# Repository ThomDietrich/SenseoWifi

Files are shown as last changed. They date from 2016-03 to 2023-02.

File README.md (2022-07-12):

# SenseoWifi - Smart Home Coffee Maker

Wifi'ify the Senseo coffee maker.

The coffee maker is with no doubt a central element of our lives.
In the Smart Home where every device is connected and automated, the coffee making can not be left out.
Let's bring the [Philips Senseo](https://de.wikipedia.org/wiki/Senseo) (Basic or Classic) into your Wi-Fi and control it remotely from your smartphone, through automation, or by extension via Alexa!

> Yes, this is silly, you should do it too!

## Summary

This project contains information and material regarding:

- Soldering a **custom PCB** needed to bring Senseo onto a Wi-Fi
- Connecting the custom PCB to the Senseo PCB
- Compiling firmware with [PlatformIO](https://platformio.org/) (e.g. as plugin in [VisualStudioCode](https://code.visualstudio.com/))
- Flashing the custom PCB with the **provided firmware**
- Connecting to Wi-Fi and [MQTT](https://www.hivemq.com/mqtt-essentials)
- Connecting to [Home Assistant](https://www.home-assistant.io), [openHAB](https://openhab.org) or any other home automation solution, including voice assistants like [Amazon Alexa](https://en.wikipedia.org/wiki/Amazon_Alexa)
- Adding a buzzer for **audio feedback** *(optional)*
- Adding a **cup detector** for further automation *(optional)*

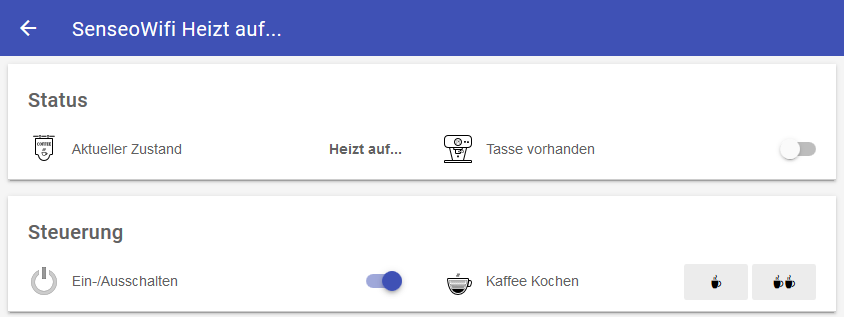
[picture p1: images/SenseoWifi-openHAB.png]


### Compatibility

This project is comatible with:

- Philips Senseo HD7810
- Philips Senseo HD7811
- Philips Senseo HD7812
- Philips Senseo HD7817
- Philips Senseo HD7865 Quadrante
- Philips Senseo HD7860 Quadrante
- … and most probably all similar models with one LED and three buttons

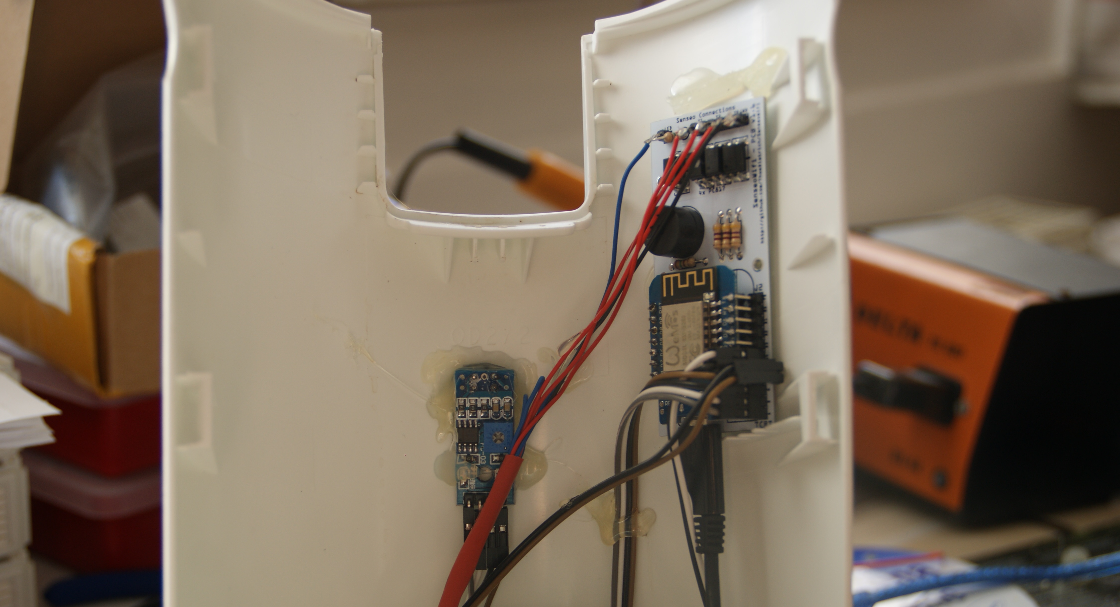
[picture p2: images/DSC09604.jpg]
installation example inside the machine


## Features

After implementing the steps below your Senseo coffee machine will offer the following new features.
This is especially useful in combination with a home automation system.

- Inform about the current state (Standby, Brewing, ...) of the machine
- Notify about an empty water tank
- Notify about a filled up coffee cup
- Remote control the machine via Wifi/MQTT commands
- Go through a complete brewing cycle automatically (Turn on, brew, turn off)
- Audio feedback via a built-in speaker
- Detect a cup via an optical sensor
- Collect usage statistics, e.g. stored in InfluxDB and visualized in Grafana

## Hardware Modification

The first challenge of this project is to hack the Senseo machine electronics.
You need to solder and connect a custom PCB to the machine.
In the end the PCB will not be visible from the outside, powered from the inside, connected via Wi-Fi and programmed over-the-air (OTA).

**⚠⚠⚠ Attention! For your own safety do not connect AC power while opened up. ⚠⚠⚠**

### Parts

| Part | Description |
|---|---|
| 1× Custom PCB | See [`SenseoWifi-PCB` folder](SenseoWifi-PCB) for schematic |
| 1× WeMos D1 Mini | Microcontroller, [learn more…](https://wiki.wemos.cc/products:d1:d1_mini) |
| 4× Sharp PC817 | Optocoupler interfacing with the Senseo board ([datasheet](http://www.sharp-world.com/products/device/lineup/data/pdf/datasheet/pc817xnnsz_e.pdf)). Thanks to these, the Senseo can be connected to AC power and to your PC via USB at the same time. Try to avoid this constellation and be cautious with active AC power. |
| 3× 470Ω Resistor | |
| 1× 1.5kΩ Resistor | |
| 1× Push button | To reset the microcontroller from the outside |
| 1× AC-DC Step Down Converter (220V to 5V) | As internally sourced power supply (e.g. [ebay.de](https://ebay.us/n9Cz6R) or [HLK-PM01](http://www.hlktech.net/product_detail.php?ProId=54)) |
| Generic male headers | A bunch of them |
| 1× Buzzer 12mm | *Optional* - Used for audio feedback, can be disabled in firmware (e.g. [reichelt.de](https://www.reichelt.de/Signalakustik/AL-60P01A/3/index.html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)) |
| 1× 150Ω Resistor | *Optional* - Size depends on buzzer |
| 1× TCRT5000 | *Optional* - To detect a cup. Reflective Optical Sensor, Regulated Module (e.g. [ebay.de](https://ebay.us/3Kf6fq)) |

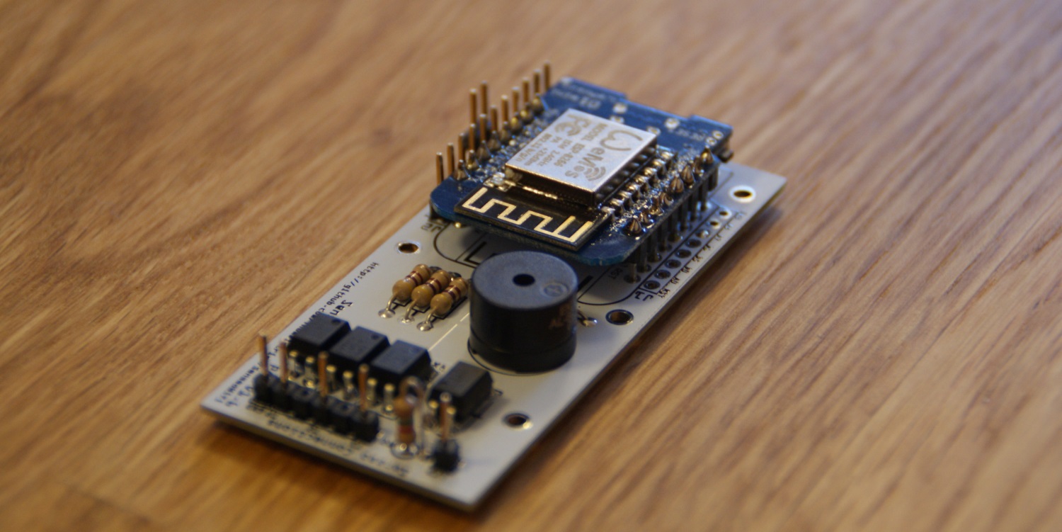
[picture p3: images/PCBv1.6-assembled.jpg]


**Power Consumption:**
The question was raised how much energy is consumed by the modification. The PCB consumes approx. 110mA.
Assuming the Senseo machine is connected to power 24/7, the additional electronics raise your electrical bill by 2.00€ per year.

### Steps

1. Solder the custom PCB according to the schematics provided in the `SenseoWifi-PCB` folder (designed in [Fritzing](http://fritzing.org))
2. Hot clue the custom PCB inside the Senseo machine in a free position [such as shown here](images/DSC09604.jpg)
3. Wire the custom PCB via the "Senseo Connections" header (angled pin headers recommended) to interface with the Senseo PCB. The solder pads to use for the LED, the buttons, and ground connection are shown on photos in the `images` folder, e.g., for the [Senseo Classic](images/DSC09627.jpg) and [Senseo Quadrante](images/SenseoQuadrante-PCB.jpg)
4. Connect a simple push button (the configuration reset button) to J3 and hot clue in the [base of the Senseo housing](images/resetbutton.jpg).
5. Connect the additional [power supply](images/DSC09646.jpg) to the Senseo power cable and wire to J4
6. Prepare a [small cutout](images/tcrt-cutout.jpg) in the Senseo front and [hot clue from behind](images/DSC09604.jpg). Connect to the TCRT header
7. Connect a USB cable to continue with firmware programming. Do not connect AC power

Please follow the details given in the schematics and the pictures in the [images](images) folder, which should make everything pretty clear.
Do not hessitate to create a support ticket on GitHub if we missed anything.
A pull request to improve this README is always welcome.

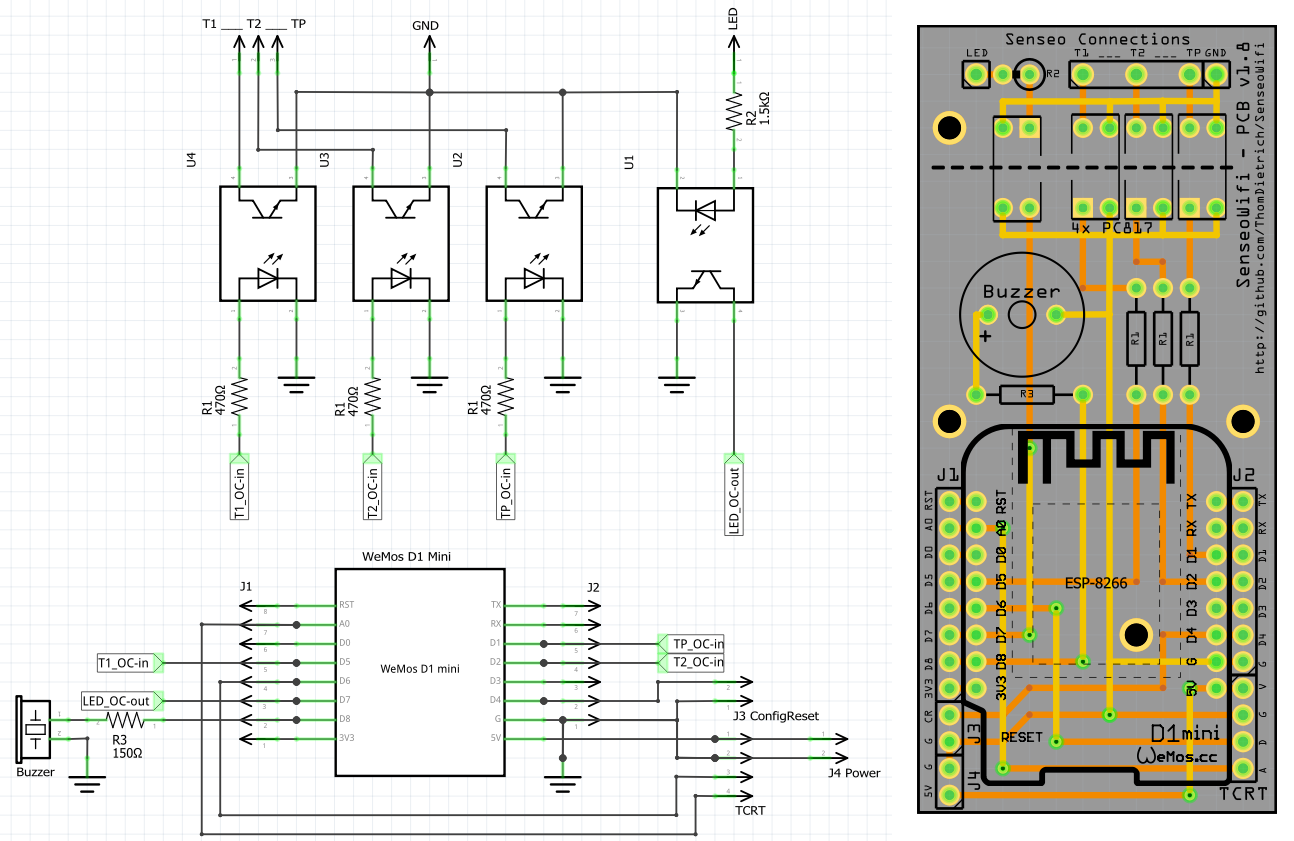
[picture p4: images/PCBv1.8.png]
schematics


## Firmware Upload

The WeMos microcontroller needs to be programmed with the code provided in this repository.
Be aware that the custom functionality is build on top of the excellent [Homie v3.0](https://github.com/homieiot/homie-esp8266/) framework.

An MQTT broker is needed in your network (e.g. mosquitto).

Please follow these instructions (last tested 2021-10-01):

1. Install PlatformIO via Visual Studio Code as decribed [here](https://platformio.org/platformio-ide) or upgrade your existing installation
2. Open PlatformIO and load a latest copy of this repository
3. Connect your Senseo via the USB cable to your PC (do not connect the Senseo to AC power!) and check the devices view of PlatformIO to verify
4. Transfer the firmware and the configuration web interface to the microcontroller.
  The full list of PlatformIO project tasks is:
   - Clean
   - Erase Flash
   - Build
   - Upload
   - Upload File System image
   - Monitor

   If any of the steps ends in a connection error dis- and reconnect the USB cable.
   You were successful when the monitoring terminal shows the SenseoWifi firmware version.
   For initial hardware testing see below.

5. Use a smartphone to connect to the provided Wifi, you will be redirected to a configuration web frontend
6. Provide your Wifi, MQTT, and other settings (we recommend the default homie base topic)
7. Use an MQTT client to inspect messages sent to the MQTT broker.
  You were successful when the message "senseo-wifi" is published to the topic `homie/senseo-wifi/machine/$name`
8. Disconnect the USB cable, close the Senseo housing, and connect the Senseo machine to AC power.
  The machine should once again start communicating via MQTT

**For Hardware testing:** A special piece of code is provided to test that your fresh hardware modifications are working.
Enable `testIO()` in `SenseoWifi.cpp` and check `testIO.cpp` for details.

**Configuration mode:** The configuration web frontend is only available when in configuration mode, i.e. when not yet configured.
Press the configuration reset button previously mounted in the base of the machine for 5 seconds to resets the firmware configuration.
The machine switches in configuration mode and provides a Wifi accesspoint, which upon connection once again presents the configuration web frontend.
Follow these instructions if you ever loose connection, or want to change your Wifi or MQTT settings.

### OTA Updates

After an initial flash with the firmware, updates can be sent via Wifi+MQTT, no need to take the machine apart.
The web frontend on flash and your custom configuration stay on the device.

```sh
python3 ota_updater_202011.py -l 192.168.0.75 -u user -d password -t "homie/" -i "senseo-wifi-rf21" .pio/build/senseo-wifi/firmware.bin
```

## Usage

If everything worked out your machine now communicates its status and accepts commands via MQTT.
You are now ready to interact with the machine and integrate it with other systems.
Please check the source code of `SenseoWifi.cpp` for details on states and commands.

## Smart Home Integration

With the machine connected to Wifi and MQTT, you can now link a smart home system to the important MQTT topics to integrate the machine with the rest of your smart home.

### Home Assistant Configuration Example

The following example integrates the Senseo machine with the home automation solution Home Assistant.
The configuration adds all necessary entities, translations to German, and clever automations to make the machine useful.
E.g. one automation enables a complete coffee brewing cycle with a single command, the other reminds you of your warm coffee every minute while you didn't pick it up.

Please make sure the machine is connected to your MQTT broker and adapt the machine name in the topic.

Home Assistant config file `packages/senseo_wifi.yaml`, see [`home-assistant/senseo_wifi.yaml`](home-assistant/senseo_wifi.yaml).

Lovelace configuration for an interactive UI control in the Home Assistant app:
```yaml
cards:
  - type: entities
    entities:
      - entity: switch.senseowifi_power
        name: Power
      - type: conditional
        conditions:
          - entity: sensor.senseowifi_opstate
            state_not: SENSEO_OFF
        row:
          entity: sensor.senseowifi_opstate
          name: Operationszustand
  - type: conditional
    conditions:
      - entity: binary_sensor.senseowifi_out_of_water
        state: 'on'
    card:
      type: entities
      entities:
        - entity: binary_sensor.senseowifi_out_of_water
          name: Wassertank leer
  - type: conditional
    conditions:
      - entity: switch.senseowifi_power
        state: 'on'
      - entity: binary_sensor.senseowifi_out_of_water
        state_not: 'on'
      - entity: binary_sensor.senseowifi_cup_full
        state: 'off'
    card:
      type: entities
      entities:
        - entity: binary_sensor.senseowifi_cup_available
          name: Tasse steht unter
  - type: conditional
    conditions:
      - entity: binary_sensor.senseowifi_cup_full
        state: 'on'
    card:
      type: entities
      entities:
        - entity: binary_sensor.senseowifi_cup_full
          name: Tasse gefüllt
  - type: conditional
    conditions:
      - entity: sensor.senseowifi_opstate
        state: SENSEO_READY
      - entity: binary_sensor.senseowifi_cup_available
        state: 'on'
      - entity: binary_sensor.senseowifi_cup_full
        state: 'off'
    card:
      type: entities
      entities:
        - type: buttons
          entities:
            - entity: input_boolean.senseowifi_brew_normal
              name: kleine Tasse brühen
              icon: mdi:coffee-to-go
            - entity: input_boolean.senseowifi_brew_double
              name: große Tasse brühen
              icon: mdi:coffee-to-go
title: SenseoWifi
type: vertical-stack
```

### openHAB Configuration Example

The following openHAB configuration allows integration of the Senseo machine with the home automation solution openHAB. Please make sure the machine is connected to your MQTT broker. Insert the MQTT broker IP and replace "senseo-wifi-home" by your device name in the below example.

The [expire binding](https://www.openhab.org/addons/bindings/expire1/) is recommended for debug-value.

**Note:** Not updated to latest firmware changes.

openHAB things file `mqtt.things`:
```
Bridge mqtt:systemBroker:LocalBroker [ host="your-broker-ip", secure=false ]
{
    Thing mqtt:topic:SenseoWiFi "SenseoWiFi" {
    Channels:
        Type string : Debug          "Debug"            [stateTopic="devices/senseo-wifi-home/machine/debug"]
        Type string : OpState        "Zustand"          [stateTopic="devices/senseo-wifi-home/machine/opState"]
        Type switch : OnOff          "OnOff"            [stateTopic="devices/senseo-wifi-home/machine/power", commandTopic="devices/senseo-wifi-home/machine/power/set", on="ON", off="OFF"]
        Type string : Brew           "Brew"             [stateTopic="devices/senseo-wifi-home/machine/brew",commandTopic="devices/senseo-wifi-home/machine/brew/set"]
        Type number : BrewedSize     "BrewedSize"       [stateTopic="devices/senseo-wifi-home/machine/brewedSize"]
        Type string : OutOfWater     "OutOfWater"       [stateTopic="devices/senseo-wifi-home/machine/outOfWater"]
        Type string : CupAvailable   "Tasse vorh."      [stateTopic="devices/senseo-wifi-home/machine/cupAvailable"]
        Type string : CupFull        "Tasse voll"       [stateTopic="devices/senseo-wifi-home/machine/cupFull"]
        Type string : Online         "Online"           [stateTopic="devices/senseo-wifi-home/$online"]

        Type string : version        "Version"          [ stateTopic="devices/senseo/$homie"]
        Type string : name           "Name"             [ stateTopic="devices/senseo/$name"]
        Type string : ip             "IP-address"       [ stateTopic="devices/senseo/$localip"]
        Type string : mac            "MAC-address"      [ stateTopic="devices/senseo/$mac"]
        Type string : fw_name        "Firmware Name"    [ stateTopic="devices/senseo/$fw/name"]
        Type string : fw_version     "Firmware Version" [ stateTopic="devices/senseo/$fw/version"]
        Type string : nodes          "Nodes"            [ stateTopic="devices/senseo/$nodes"]
        Type string : implementation "Implementation"   [ stateTopic="devices/senseo/$implementation"]
        Type string : interval       "Update interval"  [ stateTopic="devices/senseo/$stats/interval"]
    }
}
```

openHAB items file `SenseoWifi.items`:
```
String KU_Senseo_Debug         "Debug [%s]"                          {channel="mqtt:topic:SenseoWiFi:Debug", expire="10s"}
String KU_Senseo_OpState       "Zustand [MAP(senseo-wifi.map):%s]"   {channel="mqtt:topic:SenseoWiFi:OpState"}
Switch KU_Senseo_OnOff         "OnOff"                               {channel="mqtt:topic:SenseoWiFi:OnOff"}
String KU_Senseo_Brew          "Brew"                                {channel="mqtt:topic:SenseoWiFi:Brew"}
Number KU_Senseo_BrewedSize    "BrewedSize"                          {channel="mqtt:topic:SenseoWiFi:BrewedSize"}
String KU_Senseo_OutOfWater    "OutOfWater"                          {channel="mqtt:topic:SenseoWiFi:OutOfWater" [profile="transform:MAP", function="senseo-wifi.map"]}
String KU_Senseo_CupAvailable  "Tasse vorh."                         {channel="mqtt:topic:SenseoWiFi:CupAvailable" [profile="transform:MAP", function="senseo-wifi.map"]}
String KU_Senseo_CupFull       "Tasse voll"                          {channel="mqtt:topic:SenseoWiFi:CupFull" [profile="transform:MAP", function="senseo-wifi.map"]}
String KU_Senseo_Online        "Online"                              {channel="mqtt:topic:SenseoWiFi:Online"}
```

openHAB sitemap example `SenseoWifi.sitemap`:
```
sitemap testing label="Senseo-Tests"
{
    Text item=KU_Senseo_Online label="Fehler [Maschine nicht verfügbar!]" visibility=[KU_Senseo_Online == "false"] valuecolor=["false"="red"]
    Frame label="Status" visibility=[KU_Senseo_Online == "true"] {
        Text item=KU_Senseo_OpState label="Aktueller Zustand"
        Default item=KU_Senseo_Debug      label="Debug" visibility=[KU_Senseo_Debug != UNDEF] valuecolor=["red"]
        Text item=KU_Senseo_OutOfWater label="Wassertank [Leer]" visibility=[KU_Senseo_OpState == SENSEO_NOWATER] valuecolor=[ON="maroon"] icon="water"
        Switch item=KU_Senseo_CupAvailable label="Tasse vorhanden" icon="coffee_cup"
        Switch item=KU_Senseo_CupFull label="Tasse voll" visibility=[KU_Senseo_CupAvailable == ON] icon="coffee_cup_hot"
    }
    Frame label="Steuerung" visibility=[KU_Senseo_Online == "true"] {
        Switch item=KU_Senseo_OnOff label="Ein-/Ausschalten"
        Switch item=KU_Senseo_Brew label="Kaffee Kochen" mappings=[1cup="☕", 2cup="☕☕"]
    }
}
```

## Contribution

Further details outstanding. Don't hesitate to open a support issue!

Happy Hacking!

----

# Disclaimer and Legal

> *Philips* and *Senseo* are registered trademarks of *Philips GmbH*.
>
> This project is a community project not for commercial use.
> The authors will not be held responsible in the event of device failure or bad tasting coffee.
>
> This project is in no way affiliated with, authorized, maintained, sponsored or endorsed by *Philips* or any of its affiliates or subsidiaries.

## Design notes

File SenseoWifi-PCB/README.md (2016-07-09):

# SenseoWifi-PCB

this folder contains the PCB design, needed for this project.

Designed in [Fritzing](http://fritzing.org/download) (min. Version 0.9.3b, `fritzing parts` newer 2016-07-10)

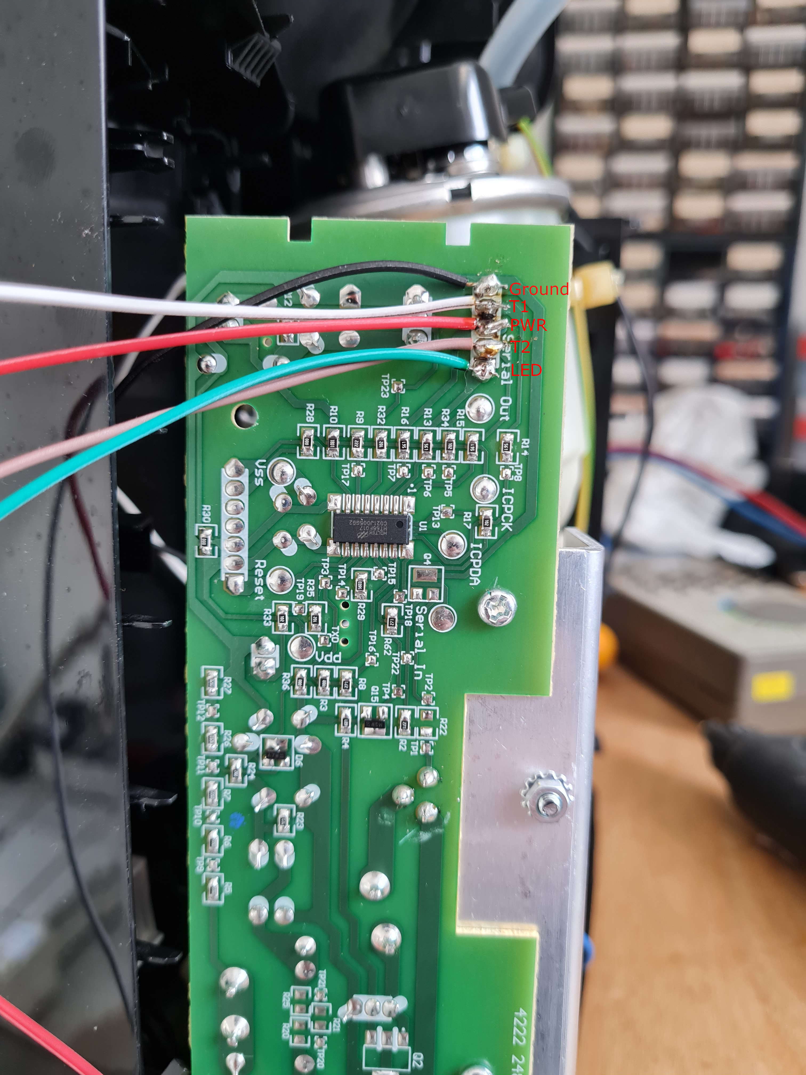
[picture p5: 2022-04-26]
images/SenseoQuadrante-PCB.jpg

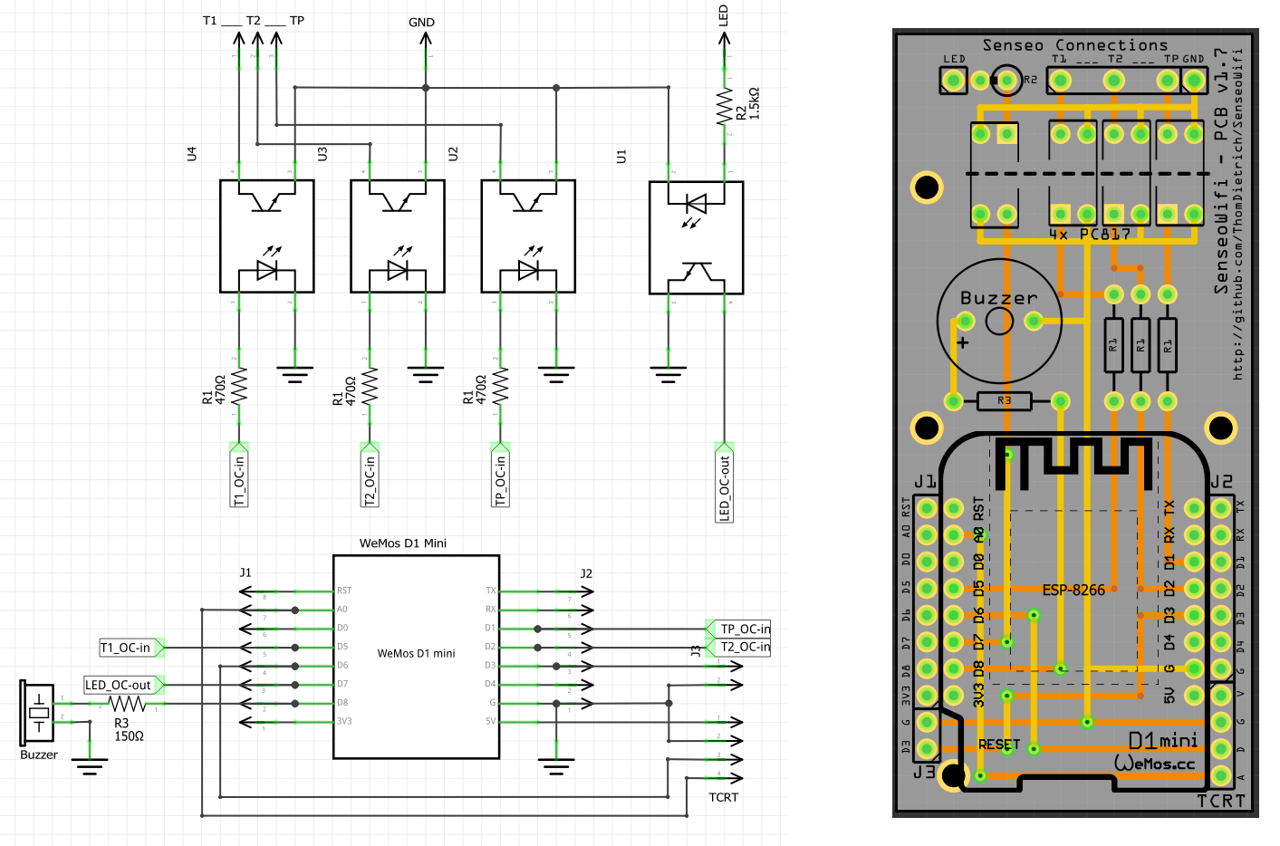
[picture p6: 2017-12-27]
images/PCBv1.7.png

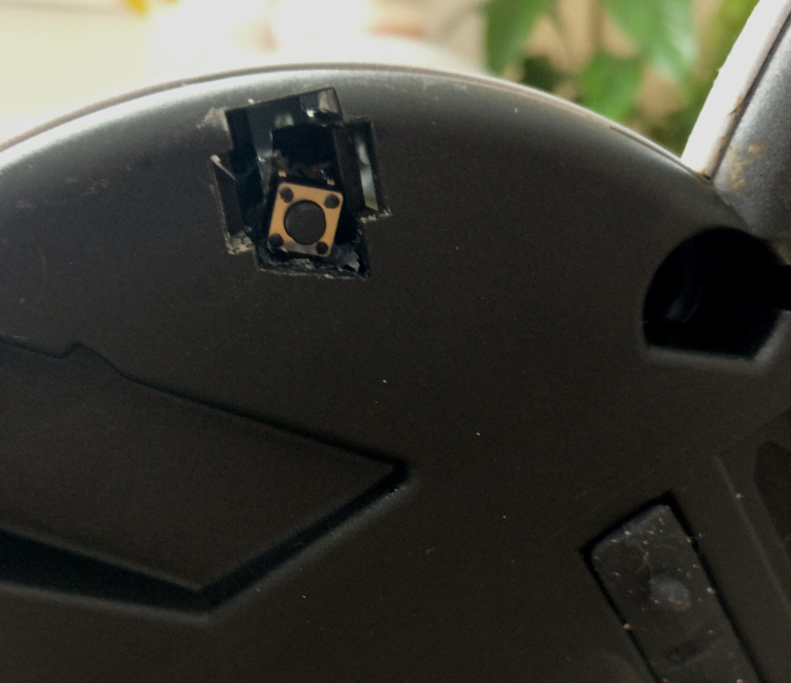
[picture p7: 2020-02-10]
images/resetbutton.jpg

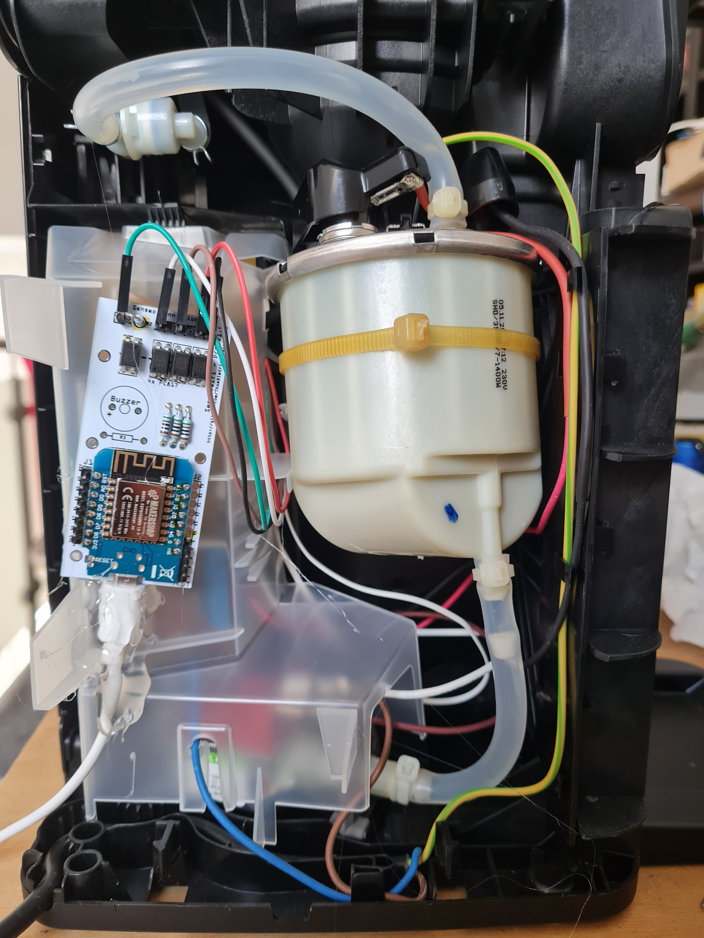
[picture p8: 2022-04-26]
images/SenseoQuadrante-Mount.jpg

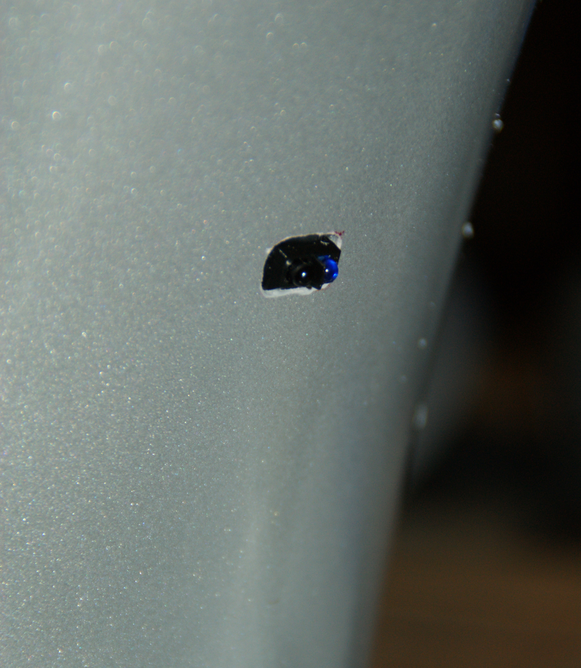
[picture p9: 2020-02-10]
images/tcrt-cutout.jpg

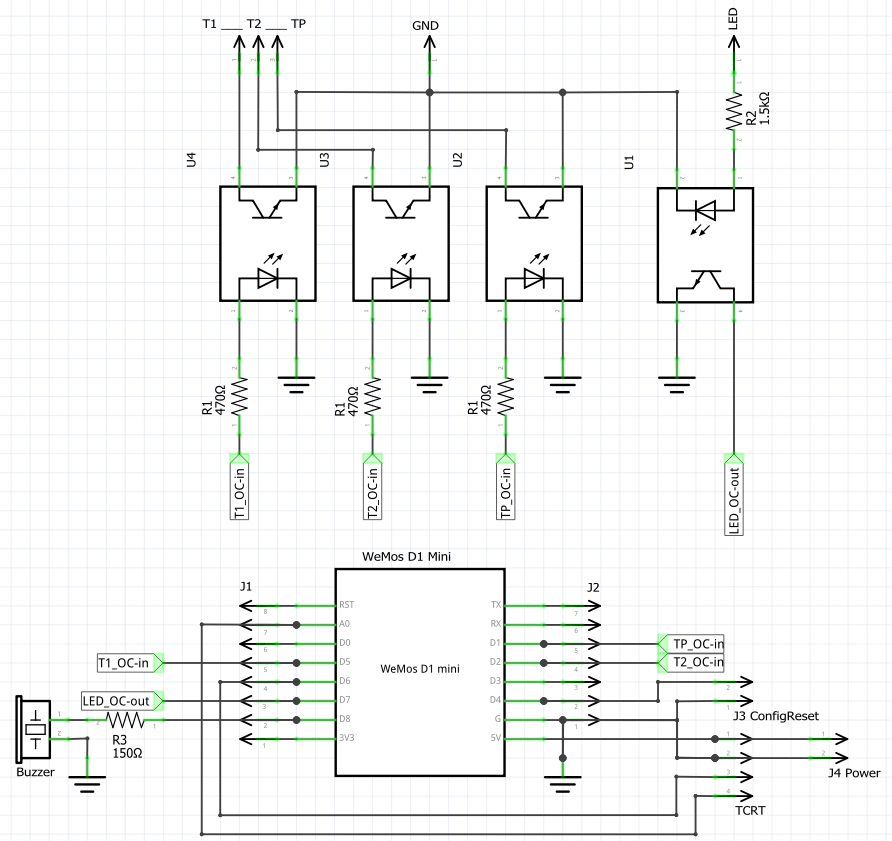
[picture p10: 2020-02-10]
images/PCBv1.8-circuit.png

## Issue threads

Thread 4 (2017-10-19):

Add README

ThomDietrich, 2017-10-19:
A README with a short description, build and usage instructions needs to be added!

@guybrushix out of coincidence I saw your forking of the repository. The README is currently missing but the PCB+code are doing their job just great since one year in two machines. Do you need any help?

guybrushix, 2017-10-20:
Thank you, I first try on my own.

VinceMasuka, 2018-09-13:
I'm doing this with FHEM instead of openHAB2. Therefore some words about the MQTT functionality would be helpful. Of course it's to be read within the src files, but a litte documentation would surely help to understand readings and commands (without misinterpretation).

fredericdepuydt, 2019-01-30:
The README file currently doesn't describe the use of PlatformIO as IDE.
Took me some time before I realized the Arduino IDE wasn't the way to program the ESP8266

mboremski, 2019-07-12:
Would also like som more advice on how to bring up.
Took me some hours of research ti find hiw to get the code onto the ESP8266.
Finally found **PlatformIO** as solution.

Than it took some time to get the right libs installed and go on with compiling.
e.g. ArduinoJson has to be 5.x.x. Seems 6.x.x does some things different and wount compile.

Than tried to monitor the connected device, but default baudrate of 9600baud issn't right
So I had to add this to platformio.ini:
`monitor_speed = 115200`

With this I have been able to debug some problems with the homie/config.json

Now I am struggeling on implementing the node in openhab.
Your device uses Homie 2.x.x, but Openhab (now) wants 3.x.x thats (as far as I could figure out) not released for esp8266.
It looks like it can be added via a *.things-File manually.
Maybe you could share the neccesary steps with us?

fredericdepuydt, 2019-07-12:
@ThomDietrich Just clarifying it's build using PlatformIO, and a link to https://platformio.org/ would suffice.

@mboremski You can take a look in the development branch of homie (https://github.com/homieiot/homie-esp8266/tree/develop-v3). I'm currently still using homie 2.0 as well, and I've added the MQTT topics manually in my OpenHAB. As for the libs, when using PlatformIO in VSCode all libs are imported automatically. The baudrate can be found in 'src/SenseoWifi.cpp': `Serial.begin(115200);` (but it wouldn't do any harm if this were added in the README as well).

Kind regards,
Frederic Depuydt

mboremski, 2019-07-12:
tried to switch to dev-v3 for homie but than got a bunch of errors I cant't handle.
e.g.
```
{
	"resource": "/d:/SenseoWifi-master/src/SenseoWifi.cpp",
	"owner": "cpp",
	"severity": 8,
	"message": "no matching function for call to 'HomieNode::HomieNode(const char [8], const char [8])'",
	"startLineNumber": 22,
	"startColumn": 42,
	"endLineNumber": 22,
	"endColumn": 42
}
```
and
```
{
	"resource": "/d:/SenseoWifi-master/src/SenseoWifi.cpp",
	"owner": "_generated_diagnostic_collection_name_#0",
	"severity": 8,
	"message": "no instance of constructor \"HomieNode::HomieNode\" matches the argument list -- argument types are: (const char [8], const char [8])",
	"startLineNumber": 22,
	"startColumn": 22,
	"endLineNumber": 22,
	"endColumn": 22
}
```
fogot to say:
espressif8266 > 2.0.4 also generates some problems.
Needed to change platform in platformio.ini to:
`platform = espressif8266@2.0.4`

would you share your files with us to help bring it up?
looking for things-file, map-file and sitemap-file(sniped)

mboremski, 2019-07-13:
Have a look at #19 to see some config-example for OH  2.4.0 ;-)

ThomDietrich, 2020-02-08:
Hey guys, I've updated the README to include flashing instructions and other details. Please open a new issue for whatever you run into

Closed 2020-02-08.

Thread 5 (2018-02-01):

Detect correct brewedSize regardless following state

ThomDietrich, 2018-02-01:
So far the information wether a small or big cup was brewed is wrongfully calculated when the machine switches into NOWATER or OFF state right after brewing. Fix to:

> Send "1" or "2" on topic `brewedSize`, regardless the following state. Otherwise send "0".

ThomDietrich, 2018-02-01:
Fixed in https://github.com/ThomDietrich/SenseoWifi/commit/7e8563480429ca54c16e6de5afd2ae5411a366e6

Closed 2018-02-01.

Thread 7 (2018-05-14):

test environment starts to beep immediately after flash

VinceMasuka, 2018-05-14:
Hi

I just rebuild your project. Right after flashing the buzzer starts to beep quiet annoying. Of corse I want to test the board before I start to integrate it into the Senseo. That's why I connect 5V and GND only to start WiFi. Although there is WiFi showing up now and I got it configured (no idea why it did not used the config.json besides), there unfortunately is this noisy beep again. Perhaps it's just my confused, deaf ears for the moment, but right now I'm kind of clueless what this thing wants to tell me...

Suggestions? Anyone?

Thanks!

Regards
Vince

ThomDietrich, 2018-05-15:
Hey!
Well that shouldn't happen but it is along time since I last flashed without a connection to the machine. Is the beeping continuous?

My suggestion would be to 1) check the serial console and/or the MQTT broker to learn about the state of the program. Besides that, 2) you could disable the buzzer in the initial configuration custom settings.

VinceMasuka, 2018-07-01:
Sorry... I was like unable to work with this project for the past several weeks...

Yes, it beeps continously. I think I leave this issue at "continous improvement process". Means that I unsoldered the beeper for silent's sake and try to get the rest running and build in the Senseo until I get back to this. Perhaps it's like you said and only an issue if it's not build in.

ThomDietrich, 2018-07-02:
I'd suggest to first connect everything and then check the serial console for debugging/log ouptut. You'll learn about the actions of the program. A constantly beeping of the beeper tells me that you probably did not yet flash my source code onto the chip. There is no continuous beeping in my code...

Closed 2020-02-08.

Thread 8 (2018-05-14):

what plug to power this

VinceMasuka, 2018-05-14:
Hi

Sorry for the maybe dumb question, but looking at the board layout, the used pins and comparing lab plus final pictures of yours...
What plug(s) are responsible for powering (5V and GND) this board?
Do you power it solely by USB?
And if so: Did you connect that USB directly to the 220V to 5V AC-DC step down module?

Thanks!

Regards
Vince

ThomDietrich, 2018-05-15:
Good question, we left the USB port open for debugging and connected the step down module directly to `GND` and `5V`. Now that you ask: I am not quite sure why there are no dedicated pins for this purpose.
Looking at the pictures, I believe that the hacked extra connectors on the side serve that purpose in our machine. https://raw.githubusercontent.com/ThomDietrich/SenseoWifi/master/images/DSC09604.jpg
If you build and soldered your own PCB, it should be easy to add additional pins. As for our provided PCB design: Yes we should improve it...

Closed 2018-07-01.

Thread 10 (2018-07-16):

Error in fz-File (fritzing 0.9.3b on Windows 10)

evildrummer, 2018-07-16:
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

ThomDietrich, 2018-07-16:
Nope sorry must be an issue with your system or download. Just tested with a fresh Fritzing and file download myself.

evildrummer, 2018-07-16:
Hm,

i tested it on Win7 and 10 (x86 and x64 Version). :-/

Can you upload a fzz or gerber version of the File? Then i dont need Fritzing anymore.
Fzz is the supported type when i want to upload it on their Website (aisler.net).

Thanks

ThomDietrich, 2018-07-16:
[SenseoWifi-PCB_GERBER.zip](https://github.com/ThomDietrich/SenseoWifi/files/2197631/SenseoWifi-PCB_GERBER.zip)

This is the file I last used to produce PCBs I'm currently using. Be aware that I realized later on that two connectors are mission in this version https://github.com/ThomDietrich/SenseoWifi/issues/8#issuecomment-389109496

ThomDietrich, 2018-07-16:
You should try once again. Your error sounds like you did something wrong when downloading the file...

evildrummer, 2018-07-16:
Well. Finally i was able to open it :)

but!..... i´m not sure if my added pins are well placed :)
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

If you´re giving me an ok i´ll do the pull request. But first i have to check out what that means :) I´m new on github.

ThomDietrich, 2018-07-16:
Looks fine to me. I myself was hoping to not extend the size of the PCB... you know what, give me a sec.

ThomDietrich, 2018-07-16:
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

ThomDietrich, 2018-07-16:
[SenseoWifi_PCB_v1.7_Extended_Gerber.zip](https://github.com/ThomDietrich/SenseoWifi/files/2198093/SenseoWifi_PCB_v1.7_Extended_Gerber.zip)

ThomDietrich, 2018-07-16:
The new connectors on the bottom left are for the Reset button and for VCC from the step down converter. Enjoy! Let me know if you need more help!

mboremski, 2019-07-20:
@ThomDietrich might be closed.. not? :-)

ThomDietrich, 2019-07-22:
Sounds like it. Thanks ;)

Closed 2019-07-22.

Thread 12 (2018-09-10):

(Improvement) Replace Step Down AC-DC Converter (220V to 5V) by Hi-Link-ac-dc

diogopms, 2018-09-10:
Note: This is not a real issue, but an improvement to the PCB.

What do you think, about changing to:
https://pt.aliexpress.com/item/Hi-Link-ac-dc-power-module-5v-3w-220v-isolated-ac-dc-converter/32360232521.html

VinceMasuka, 2018-09-13:
Works flawlessly. I took the same on my setup.
[http://www.hlktech.net/product_detail.php?ProId=54](url)

ThomDietrich, 2018-11-21:
Looks good indeed. Why would you recommend this one over the one I've linked?

VinceMasuka, 2018-12-17:
Perhaps because it comes in a enclosure?
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
(inside it's pretty much the same, I guess)

Actually that might be preferable of sorts, as there is water around and you might would like the idea of some extra "shielding"...

ThomDietrich, 2018-12-17:
Fine by me. Please create a PR against the README.md as an alternative product in the components table.

Ditoxius, 2019-01-17:
Hi, i have another question regarding the supply voltage.

The senseo µC is powered the whole time with 5V via a capacitive divider and zener diode. Have you tried using its supply voltage to power the WeMos module instead of installing a separat step-down converter?

Thank you for your project....i hope to make my coffee maker smart, soon :D

ThomDietrich, 2019-01-18:
Yes. I tried and I did a few thought experiments on the topic with colleagues. The problem is (please correct me if you disagree) that such a circuit has a narrow operating point and experiments showed that voltage drops as soon as more than a few milliamps are consumed.

Another problem is the missing divide of electrical potentials between the Senseo supply and the USB connection (think optocouplers).

I very much prefer the decoupled solution for its simplicity and the flexibility in build in troubleshooting. Lastly and maybe most importantly: The solution comes as safe as it can get (I hope :) ).

Closed 2019-01-18.

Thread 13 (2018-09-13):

current on the buttons

VinceMasuka, 2018-09-13:
Hi...

I tried to get this project finally done and everything is now build in the Senseo:

- MQTT nicely reports the readings

- MQTT readings instantly update themselves when you send a MQTT command or

- MQTT readings instantly update themselves when press a button on the Senseo

But:

- a MQTT send "power" to the board reports that Senseo is powered, but it won't turn on (harware button works of course)

- strangely all buttons on the board (TP, T1, T2) allways have current of exactly 5.08 volts (no matter if MQTT says they are on or not) (I expected something like 0 volts when it's turned off)

By any chance you can't push me in the right direction what to check first?

Thanks!

Regards
Vince

ThomDietrich, 2018-11-21:
Hey Vince!
Sorry for the late reply. Did you solve the issue?

ThomDietrich, 2018-12-14:
Hey!
Just to summarize:

1. You receive MQTT messages from the board and therefore are certain that the firmware flash worked.
2. More precisely, you receive "ON" via `.../power` and "SENSEO_HEATING" via `.../opState` if you press the power button manually?
3. You publish a message with payload "ON" to the topic `.../power/set` and "MQTT reports back" - what do you mean by that? As you can see [here](https://github.com/ThomDietrich/SenseoWifi/blob/master/src/SenseoWifi.cpp#L45) there is no optimistic response. The response should be what's described under (2.). For testing please send an invalid payload and check for the "power: malformed message content." debugging message.

To rule out hardware issues you could modify the source code to trigger a power press, e.g., when the firmware has booted.

ThomDietrich, 2018-12-14:
FYI:
Try to get it working with MQTT first. That is best for troubleshooting.
For later use you might be happy to find my openHAB configuration here: https://github.com/ThomDietrich/openhab-config/blob/master/items/senseoWifi.items
Don't torture yourself with FHEM 😅

VinceMasuka, 2018-12-16:
1. I really like to belive that.
2. Yes, that works as expected. If I manually push the button physically on the Senseo, my mosquitto_sub tells me "opState SENSEO_HEATING", "power ON", "outOfWater false", "brew false" and "opState SENSEO_READY".
3. Oh, I just meant if I publish something, that the mosquitto subscription immediately tells me so (as expected). So when I send a invalid content like
"mosquitto_pub -t homie/Senseo/machine/power/set -m toggle"
I receive:
"debug power: malformed message content. Allowed: [ON,OFF]"

That brings us to the assumed valid version:
mosquitto_pub -t homie/Senseo/machine/power/set -m ON
...but "opState" stays on "SENSEO_OFF".

ThomDietrich, 2018-12-16:
So far so good. Now I'm afraid you need to modify the source code to figure out where the issue lies exactly.

VinceMasuka, 2018-12-17:
OK, for the sake of progress, I'll have to do so...

So this suggestion implies that you think this is not hardware, but software related?

ThomDietrich, 2018-12-17:
To the contrary. As the firmware seems to work and interact with your machine (it's able to detect "power ON") this is most probably an issue with your hardware setup. You need to follow along the route, make sure the optocoupler is swithced and check why it doesn't trigger a Senseo button press. One thing you could do: Increase the milliseconds of virtual button press, then measure the optocoupler on output side. Whatever you do please be careful with high voltage.

VinceMasuka, 2018-12-18:
Nice hint. I modified the virtual button press to 1000 an voila: Senseo is powering up.

Thanks!

ThomDietrich, 2018-12-19:
Wonderful. Would you invest a few extra minutes to figure out which lowest value would work for you? I'd like to update the source code here accordingly but one full second is quite a lot. How about e.g. 150 or 200?

VinceMasuka, 2018-12-19:
As to your pictures and decriptions, having your project as example for mine, I directly added an external micro usb access to my 7820 Senseo, too. This makes flashing pretty easy now and I'll do some more flashes (see my open TCRT issue). With this upcomming flashing, I'll alter the virtual press button and report back within this thread.

ThomDietrich, 2018-12-19:
Thanks! Your help will make a rebuild easier for the next guy.

I need to update documentation. I know that it does not at all cover all aspects of the project.
Regarding OTA I can tell you that you need to follow the OTA mechanism of homie-esp8266:

* http://marvinroger.github.io/homie-esp8266/docs/stable/others/ota-configuration-updates/

If the script doesn't work for you check out this bash script: https://github.com/marvinroger/homie-esp8266/issues/308

VinceMasuka, 2018-12-21:
I don't know what went wrong in first place, but it now seems that my setup accepts much lower ms for the virtual button press than before (I'm starting to suspect a faulty copper wire in there...).

Anyhow it looks like that
    _static const int pressDuration = 36;_
is the lowest working value with the Seseno 7820.

mboremski, 2019-07-15:
Not sure if this still is open..
I also had some issues to get the buttons "pressed" via OP.
For me 110ms have been the lowest value it was working with.
I would recommend to change it to:

```cpp
// Duration of button "press" (in milliseconds)
static const int pressDuration = 150;
```

ThomDietrich, 2019-07-19:
It is probably safe to assume that this change will not have any side effects. I would be most curious to know why this is an issue for you guys. Do you own an older/newer Senseo model or did you use different optocouplers?

mboremski, 2019-07-20:
From my knowledge of µC coding it **might** be possible that Senseo changed the time a button needs to be pressed. Maybe for better antibeat performance.
I think the 100ms has been a bit to tight to fir for all devices.

Did you once try to shorten your `pressDuration` to find the minimum pressing-time for your Senseo?
Could be that 90ms already is to short. In this case the 100ms are to tight to adress also manufacturing-tolerances.

ThomDietrich, 2019-07-22:
I probably did. My initial tests to understand the behavior of the machine were pretty thorough. Can't remember though and your 90ms argument could just as well be true. 150 is a worthy improvement 👍

Closed 2019-07-22.

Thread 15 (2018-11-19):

publishes to MQTT but does not receive

vogler, 2018-11-19:
I'm using home-assistant's embedded MQTT broker. The esp8266 publishes topics like `opState` and `debug`, but doesn't receive any commands. My Tasmota devices receive commands via MQTT jut fine.
Publishing `foo` to `devices/senseo-wifi/machine/power` should result in an output on `devices/senseo-wifi/machine/debug`, but doesn't do anything.
How can I debug this?

vogler, 2018-11-19:
Ok, just found out it's actually `devices/senseo-wifi/machine/power/set`. Works 😄
Maybe a sentence in the readme on how to test it would be a good idea.

ThomDietrich, 2018-11-21:
The README does not explicitly state that but the device follows the Homie convention. Check it out for all details! ;)

I'll need to update the README with a lot of things. Anything else you found? Does your machine work? Btw if you are located in Germany I could send you one of my spare PCBs.

ThomDietrich, 2018-11-22:
Hey!
You can leave USB connected for debugging, that is the main reason for the optocouplers.

What concerns me is the picture of your machine. It seems to be an older model. Could you tell me the exact type number?
Nevertheless, as the PCB just observes the LED and digitally pushed the buttons I believe it should still work. I would suggest to connect USB, then go through a bit of testing. You should see *very precise* timings of +-1ms. See: https://github.com/ThomDietrich/SenseoWifi/blob/master/src/constants.h#L12 for the times.

> but now I also get values like 6 and 285

Please check again. If those are your readings there is probably something wrong with your PCB or power supply.

If your Senseo PCB is older, this could also be an issue with a less stable LED power supply. Be careful while playing around with this part of the problem!!

Please keep me in the loop!

Also: Any addition to the readme, the source code or the PCB is highly welcome!!

vogler, 2018-11-22:
It's a Philips HD 7801/62.
Everything worked fine for the first brew. I found out that now `ledChangedHandler` seems to fire whenever `cupAvailable` changes. When I remove the TCRT5000 it doesn't change states anymore.

I use the following times:
~~~
pulseDurLedSlow = 1000;          
pulseDurLedFast = 80;            
pulseDurTolerance = 30;          
pulseContThreshold = 2 * pulseDurLedSlow;

HeatingTime = 70; // cold start -> LED blinks -> LED on
HeatingTimeTol = 10;
Brew1CupSeconds = 34; // warmed up: LED on -> LED blinks -> LED on
Brew2CupSeconds = 70; // "
BrewHeat1CupSeconds = 64; // HeatingTime+Brew1CupSeconds
BrewHeat2CupSeconds = 140; // HeatingTime+Brew2CupSeconds
~~~
It wasn't exactly clear to me what the difference is, are the comments right?

ThomDietrich, 2018-11-27:
Before working with the recipe feature I'd recommend to find out if the rest does what it is supposed to. If the TCRT5000 seems to be part of the issue could you please check if the problem is on PCB or code side?

Regarding the times: Are you sure your changes are correct? Does your machine really have a fast blinking period of 80?

The comments are not clear indeed. Please create a PR ;) See here: https://github.com/ThomDietrich/SenseoWifi/blob/master/src/SenseoWifi.cpp#L139 BrewHeat is the normal cycle from pressing the brew button till the machine is finished and the LED stops blinking. The brew times represent the first part of those if the machine switches to OFF or NOWATER after brewing.

evildrummer, 2018-12-29:
Ich hätte gerne das übrige pcb abgekauft :)

Closed 2020-02-08.

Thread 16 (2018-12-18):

TCRT5000 switched

VinceMasuka, 2018-12-18:
Hi there

I wired everything with a TCRT5000 connected to the "main" board. Funny thing is, that without cup both leds on the TCRT are on and the MQTT subscription says
_(...)/cupAvailable true_

Now when I put a cup in place, the LED on the A0 side turns off and MQTT reports
_(...)/cupAvailable false_

Now shouldn't be that the other way around (at least the MQTT reporting)?

ThomDietrich, 2018-12-19:
Most certainly 😄 My best guess is that you've bought a module that behaves differently than mine ([compare here](https://www.ebay.de/itm/TCRT5000-Reflektierende-IR-Lichtschranke-Optisch-Sensor-Modul-Arduino-Raspberry/252795025375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)).

I believe you just need to remove the "!" from those two lines: https://github.com/ThomDietrich/SenseoWifi/blob/master/src/Cup.cpp#L12-L16

ThomDietrich, 2018-12-19:
Btw you might want to activate this to test everything: https://github.com/ThomDietrich/SenseoWifi/blob/master/src/SenseoWifi.cpp#L340-L346

VinceMasuka, 2018-12-21:
Awesome: "We have a bingo here!"

Somehow I just thought a TCRT5000 would be a TCRT5000, but how could I... Well, this one is mine:
[https://www.amazon.com/WINGONEER-TCRT5000-Infrared-Reflectance-Avoidance/dp/B01DCZA6RG](url)
(and it likes to have the exclamation marks out there)

Thanks a lot!

Closed 2018-12-21.

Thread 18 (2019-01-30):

Feature request: Toggle cup detection sensor

fredericdepuydt, 2019-01-30:
Hi,

A recently started creating this project myself, and was wondering how to minimize the power consumption. I'm suspecting the cup detection will be lit 24/7, but the actual detection only needs milliseconds to determine if there's a cup or not.

Wouldn't it be interesting to have a digital output pin controlling the input voltage of the TCRT5000 module?

Kind regards,
Frederic

ThomDietrich, 2019-07-15:
Hey Frederic,
did you measure the current on the module? Even with the LED it's probably just a few milliamps and would cost you literally cents :) To be fair I never measured the consumption of the whole setup. Would be interesting to know which difference the added components make relative to the normal standby consumption of the Senseo.
Regarding the LEDs: Did you consider disconnecting it?

fredericdepuydt, 2019-07-15:
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

I haven't measured it yet, I'll do some measurements when my project is finished ;) I'll be using an IR led with a transistor and an IR sensor with a transistor. This allows me to first measure the ambient light, and afterwards compare the value when the IR led is turned on.

This measurement would only take several milli seconds, and during idle times both transistors would be turned off. I'll share the schematics and code when it's finished.

ThomDietrich, 2019-07-16:
> I haven't measured it yet, I'll do some measurements when my project is finished ;) I'll be using an IR led with a transistor and an IR sensor with a transistor. This allows me to first measure the ambient light, and afterwards compare the value when the IR led is turned on.

The TCRT5000 also has an analog out, giving you a comparable measurement. Then you can simply check for differences and thereby identify the cup. I won't stop you, not sure if it's worth it :) If you want to improve something it would be interesting to learn about a solution that is more easier to install and maintain. Cutting the hole for the two LEDs and keeping them clean is not easy. I would love a sensor that is e.g. housed in one round shape and flush with the senseo surface...

In any case: Yes definitely share your findings! :)

mboremski, 2019-07-20:
I have been corius and measured the current of the TCRT5000:
Without cup: 25.7mA
With cup: 28.9mA

So the Sensor is taking approx. 145mW continuously.
This leads to 1.27kWh per year.
That is in germany around 0,4€/year. ;-)

ThomDietrich, 2019-07-22:
Thanks @mboremski !!

> The whole PCB is taking around 110mA (including TCRT5000)

would you like to add this to our README? I can see others raising similar questions.

ThomDietrich, 2020-02-08:
Even if measurements by @mboremski are not correct, I guess it is safe to assume that this is not a real issue. I've added a note to the README. https://github.com/ThomDietrich/SenseoWifi/commit/fc12187822dca027e2fcc0dc260cb7dc9552dedc

Closed 2020-02-08.

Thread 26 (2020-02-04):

Problem beim compelieren

diskus-tempel, 2020-02-04:
Hello I try the d1zu flashing but without success he has problems with the firmware

```
_-----------------------
GED_FW_NAME, __FLAGGED_FW_VERSION);

                                                                                             ^
src \ SenseoWifi.cpp: 352: 3: note: in expansion of macro 'Homie_setFirmware'
   Homie_setFirmware ("senseo-wifi-wemos", senseoWifiFWVersion);
   ^
*** [.pio \ build \ d1_mini \ src \ SenseoWifi.cpp.o] Error 1
```

I'm not getting anywhere, there is a tip for me here

ThomDietrich, 2020-02-04:
Hallo Diskus-tempel,
wenn du möchtest können wir gern auf Deutsch reden.
Dein Ausschnitt reicht mir leider noch nicht. Kannst bitte die komplette Ausgabe hier her kopieren?

Normalerweise stammt ein solcher Fehler immer von einer fehlerhaften Konfiguration ab oder es werden die falschen Versionen der gelinkten Bibliotheken verwendet. Kannst du bitte deine Bibliotheken prüfen? Poste gern so viel wie du kannst hier.

Ergänzung: Vermutlich liegt es an der Homie Version. Ich muss den Code hier dringend auf den aktuellen Stand bringen.
Probiere bitte das folgende in platformio.ini:
```ini
lib_deps = https://github.com/homieiot/homie-esp8266.git#v2.2
```

diskus-tempel, 2020-02-04:
Hi , gut das ich auch in deutsch schreiben kann ,
ich habe in die ini nun folgendes rein
`lib_deps = https://github.com/homieiot/homie-esp8266.git`
nun Fehlert das compelieren an anderen stellen

`> Executing task: C:\Users\pcwasser\.platformio\penv\Scripts\platformio.exe run <

Processing d1_mini (platform: espressif8266@2.0.4; board: d1_mini; framework: arduino)
-------------------------------------------------------------------------------------------------------------------------
Verbose mode can be enabled via `-v, --verbose` option
CONFIGURATION: https://docs.platformio.org/page/boards/espressif8266/d1_mini.html
PLATFORM: Espressif 8266 2.0.4 > WeMos D1 R2 and mini
HARDWARE: ESP8266 80MHz, 80KB RAM, 4MB Flash
PACKAGES: toolchain-xtensa 1.40802.0 (4.8.2), framework-arduinoespressif8266 2.20500.190223 (2.5.0), tool-esptool 1.413.0 (4.13)
LDF: Library Dependency Finder -> http://bit.ly/configure-pio-ldf
LDF Modes: Finder ~ chain, Compatibility ~ soft
Unicode decode error has occurred, please remove invalid (non-ASCII or non-UTF8) characters from C:\Users\pcwasser\.platformio\packages\framework-arduinoespressif8266\libraries\ESP8266HTTPUpdateServer\library.properties file
Unicode decode error has occurred, please remove invalid (non-ASCII or non-UTF8) characters from C:\Users\pcwasser\.platformio\packages\framework-arduinoespressif8266\libraries\ESP8266HTTPUpdateServer\library.properties file
LibraryManager: Installing homie-esp8266
git version 2.25.0.windows.1
Cloning into 'c:\Users\pcwasser\Desktop\SenseoWifi-master\SenseoWifi-master\.pio\libdeps\d1_mini\_tmp_installing-0chtt7q7-package'...
PermissionError: [WinError 5] Zugriff verweigert: 'c:\\Users\\pcwasser\\Desktop\\SenseoWifi-master\\SenseoWifi-master\\.pio\\libdeps\\d1_mini\\_tmp_installing-0chtt7q7-package\\.git\\objects\\pack\\pack-572729e78668a4b9d3c938efeab33fe4b556aed4.idx':
  File "C:\Users\pcwasser\.platformio\penv\lib\site-packages\platformio\builder\main.py", line 151:
    env.SConscript("$BUILD_SCRIPT")
  File "C:\Users\pcwasser\.platformio\packages\tool-scons\script\..\engine\SCons\Script\SConscript.py", line 605:
    return _SConscript(self.fs, *files, **subst_kw)
  File "C:\Users\pcwasser\.platformio\packages\tool-scons\script\..\engine\SCons\Script\SConscript.py", line 286:
    exec(compile(scriptdata, scriptname, 'exec'), call_stack[-1].globals)
  File "C:\Users\pcwasser\.platformio\platforms\espressif8266\builder\main.py", line 267:
    target_elf = env.BuildProgram()
  File "C:\Users\pcwasser\.platformio\packages\tool-scons\script\..\engine\SCons\Environment.py", line 224:
    return self.method(*nargs, **kwargs)
  File "C:\Users\pcwasser\.platformio\penv\lib\site-packages\platformio\builder\tools\platformio.py", line 140:
    _build_project_deps(env)
  File "C:\Users\pcwasser\.platformio\penv\lib\site-packages\platformio\builder\tools\platformio.py", line 48:
    project_lib_builder = env.ConfigureProjectLibBuilder()
  File "C:\Users\pcwasser\.platformio\packages\tool-scons\script\..\engine\SCons\Environment.py", line 224:
    return self.method(*nargs, **kwargs)
  File "C:\Users\pcwasser\.platformio\penv\lib\site-packages\platformio\builder\tools\piolib.py", line 1027:
    project.install_dependencies()
  File "C:\Users\pcwasser\.platformio\penv\lib\site-packages\platformio\builder\tools\piolib.py", line 859:
    lm.install(uri)
  File "C:\Users\pcwasser\.platformio\penv\lib\site-packages\platformio\managers\lib.py", line 301:
    force=force,
  File "C:\Users\pcwasser\.platformio\penv\lib\site-packages\platformio\managers\package.py", line 696:
    pkg_dir = self._install_from_url(name, url, requirements, track=True)
  File "C:\Users\pcwasser\.platformio\penv\lib\site-packages\platformio\managers\package.py", line 497:
    return self._install_from_tmp_dir(_tmp_dir, requirements)
  File "C:\Users\pcwasser\.platformio\penv\lib\site-packages\platformio\managers\package.py", line 583:
    shutil.move(tmp_dir, pkg_dir)
  File "C:\Users\pcwasser\.platformio\python37\lib\shutil.py", line 578:
    rmtree(src)
  File "C:\Users\pcwasser\.platformio\python37\lib\shutil.py", line 516:
    return _rmtree_unsafe(path, onerror)
  File "C:\Users\pcwasser\.platformio\python37\lib\shutil.py", line 395:
    _rmtree_unsafe(fullname, onerror)
  File "C:\Users\pcwasser\.platformio\python37\lib\shutil.py", line 395:
    _rmtree_unsafe(fullname, onerror)
  File "C:\Users\pcwasser\.platformio\python37\lib\shutil.py", line 395:
    _rmtree_unsafe(fullname, onerror)
  File "C:\Users\pcwasser\.platformio\python37\lib\shutil.py", line 400:
    onerror(os.unlink, fullname, sys.exc_info())
  File "C:\Users\pcwasser\.platformio\python37\lib\shutil.py", line 398:
    os.unlink(fullname)
============================================== [FAILED] Took 5.42 seconds ==============================================
The terminal process terminated with exit code: 1

Terminal will be reused by tasks, press any key to close it.`

in der fehlerhaften datei ist folgende zeile
`HomieNode senseoNode("machine", "machine");`

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

diskus-tempel, 2020-02-04:
und mit dem alten github link macht er folgendes

`> Executing task: C:\Users\pcwasser\.platformio\penv\Scripts\platformio.exe run --target upload <
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
diskus-tempel, 2020-02-05:
guten abend zusammen
ich habe nun wieder einige stunden damit verbracht ich komme hier nicht weiter derzeit :(

ich habe das UI-Bundle auch in die verzeichnisse rein geladen .
ob das spiff uploade ist oder nicht weis ich leider nicht !

ich hab meinen wemos nun bestimmt zum 500 mal geflasht . und ich habe immer das selbe ergebnis

ich habe homie version 2.0 gefunden auch diese ohne erfolg :(

lg sven

diskus-tempel, 2020-02-05:
email ist raus

ThomDietrich, 2020-02-08:
Hey Sven,
ich habe das Projekt einmal mehr oder weniger komplett überarbeitet. Die Firmware setzt jetzt auf Homie 3 und alles ist entsprechend angepasst. Ich hab auch eine gute Stunde in die README investiert um das Flashen mit PlatformIO zu beschreiben. Bin gespannt ob du damit klar kommst.

Die Platine ging übrigens am Donnerstag raus. Hast du sie bereits erhalten?

diskus-tempel, 2020-02-08:
Hi

Cool werde ich wenn ich es schaffe morgenabend mal ansehen,  bin heute nicht mehr zuhause.

Die platine ist heute gekommen :)

Evtl schaff ich es nachher mal die readme zu lassen.
Sag dir aber nochmal bescheid,  also wenn ich es morgen schaf!

Lg und danke das du fur mich alles umgestrikt hast.

--
Diese Nachricht wurde von meinem Android Mobiltelefon mit GMX Mail gesendet.Am 08.02.20, 18:06 schrieb Thomas Dietrich <notifications@github.com>:

  Hey Sven, ich habe das Projekt einmal mehr oder weniger komplett überarbeitet. Die Firmware setzt jetzt auf Homie 3 und alles ist entsprechend angepasst. Ich hab auch eine gute Stunde in die README investiert um das Flashen mit PlatformIO zu beschreiben. Bin gespannt ob du damit klar kommst.
  Die Platine ging übrigens am Donnerstag raus. Hast du sie bereits erhalten?
  —You are receiving this because you modified the open/close state.Reply to this email directly, view it on GitHub, or unsubscribe.

diskus-tempel, 2020-02-09:
Hi,  hab jetzt wieder versucht die software /firmware zu laufen auf meinen d1 hab wieder das problem das es unterlagen zum ap nicht geht :(
--
Diese Nachricht wurde von meinem Android Mobiltelefon mit GMX Mail gesendet.Am 08.02.20, 18:06 schrieb Thomas Dietrich <notifications@github.com>:

  Hey Sven, ich habe das Projekt einmal mehr oder weniger komplett überarbeitet. Die Firmware setzt jetzt auf Homie 3 und alles ist entsprechend angepasst. Ich hab auch eine gute Stunde in die README investiert um das Flashen mit PlatformIO zu beschreiben. Bin gespannt ob du damit klar kommst.
  Die Platine ging übrigens am Donnerstag raus. Hast du sie bereits erhalten?
  —You are receiving this because you modified the open/close state.Reply to this email directly, view it on GitHub, or unsubscribe.

diskus-tempel, 2020-02-09:
Guten abend herr dietrich,.

Ich habe es jetzt auf 4 computer versucht. Und auch mit der neuen version,
Ich bekomm dennoch den ui bundle fehler :(

Ich finde den fehler nicht wo ran es liegt.

Gibt es eine datei um den config modus zu stoppen und eine wlan datei um das zum um gehen.  Oder haben sie die moglichkeit mir via teamwiever zu helfen?

Ich bin da langsam an den punkt wo ich nicht mehr weiter weis,  da ich sogar auf mehreren computern immer den selben fehler bekomm :(

Lg sven
Guten start in die neue woche!
--
Diese Nachricht wurde von meinem Android Mobiltelefon mit GMX Mail gesendet.Am 08.02.20, 18:06 schrieb Thomas Dietrich <notifications@github.com>:

  Hey Sven, ich habe das Projekt einmal mehr oder weniger komplett überarbeitet. Die Firmware setzt jetzt auf Homie 3 und alles ist entsprechend angepasst. Ich hab auch eine gute Stunde in die README investiert um das Flashen mit PlatformIO zu beschreiben. Bin gespannt ob du damit klar kommst.
  Die Platine ging übrigens am Donnerstag raus. Hast du sie bereits erhalten?
  —You are receiving this because you modified the open/close state.Reply to this email directly, view it on GitHub, or unsubscribe.

ThomDietrich, 2020-02-10:
Hallo,
ruf mich doch bitte gegen 19 Uhr an. 0173/6152492

ThomDietrich, 2021-10-04:
Hallo,
ich habe heute ein paar Kleinigkeiten verändert und das Kompilieren und Hochladen erfolgreich ohne Probleme hinbekommen. Wollt ich nur erwähnen falls es dich interessiert ;) lg

Closed 2021-10-04.

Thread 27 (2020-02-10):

Additional audio feedback

ThomDietrich, 2020-02-10:
To make debugging easier/more transparent:
- [x] when powered on
- [ ] when connected to Wifi
- [x] when connected to MQTT broker
- [ ] first time machine is ready to brew (??)

Ideas or comments?

Closed 2021-10-04.

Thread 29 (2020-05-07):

Arduino Core fix

ThomDietrich, 2020-05-07:
@pattyland  wrote in https://github.com/ThomDietrich/SenseoWifi/pull/28:

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

ThomDietrich, 2020-05-07:
@pattyland did you try the `ICACHE_RAM_ATTR` workaround?

pattyland, 2020-05-08:
No, it was late at night and pinning the platform version was quicker 🙈

Closed 2020-05-11.

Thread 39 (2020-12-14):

Compatibility question

kennhardy, 2020-12-14:
Hi, would love to test this modification on my Sensei Switch HD6594/60. Do you think it might work? Mostly the electronics / schematis are needed to work. If code needs adjusting I might hopefully figure those out.

ThomDietrich, 2020-12-16:
Hey!
I had a quick look at the manual. The machine seems to have three buttons for the three different modes. Furthermore it has a "Calc light". What I am not quite sure of: Does every button have it's own LED? Please let me know so we can check that enough I/O ports are available.

So here it goes. The code and instructions here can definitely be used! You need to add the additional buttons and LEDs to the circuit and modify the logic to account for the different modes. I don't see any real issues here. Also, you should be able to get one-two modes working by leveraging the existing logic right away. This way you can start testing, get it working, and go from there.

Let me know what you decide! Best! Thomas

When you start working on this project remember to be careful with the open circuit. At least in the classic Senseo, most if it is connected to AC.

kennhardy, 2020-12-16:
Hi there @ThomDietrich! Thank you for replying so promptly.

The machine has three buttons and three led's - one for each button. Each button do specific tasks based on what you want (3in1).

Buttons in order back to front:
 - Brew pot of coffee, with filter
 - Brew big cup of coffee, big cartridge used
 - Brew medium cup of coffee, small cartridge used. This button also has a double-click feature which brews a even smaller cup coffee, more like an espresso.

For me, automating the morning coffee - two buttons / features would suffice since I only fetch one cup on my way out the door. But if you'd like to support this machine with all features i'd gladly purchase the necessary parts and provide you with any needed information about it.

Have a nice one and merry christmas to you!

ThomDietrich, 2021-10-04:
Hey, sorry I never got back to you. What did you end up doing? With all the buttons and LEDs the first problem that came to mind is the lack of IO pins on the Wemos...

Closed 2021-11-14.

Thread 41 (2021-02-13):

Implementing in Home Assistant

Post404, 2021-02-13:
Everything in this project has been new for me, soldering, ordering a custom PCB, dealing with firmware. I am now at the point that i'm trying to implement it into Home Assistant. It is connected to the Wifi and to the MQTT broker.
I just don't know how to "translate" the OpenHAB config to Home Assistant. Is there any example available that I can see?

ThomDietrich, 2021-02-15:
Hey @Post404,
I was happy to read that you were able to bring your Senseo to the point where you can read its status and send commands via MQTT. Correct? Congrats!

Please provide any issue you had or details that was missing from the description. I can certainly add more content to the README of this project.

----

I've also recently hooked my SenseoWifi to HomeAssistant. The current firmware does not support Home Assistant auto discovery via MQTT but that is on my low prio todo list. Till then you can use the following configuration as a starting point:

If you didn't already, activate the [packages concept](https://www.home-assistant.io/docs/configuration/packages/) in Home Assistant's `configuration.yaml` (this is not strictly linked to the below but is imho a must for all HA setups):

```yaml
homeassistant:
  ...
  packages: !include_dir_named packages
```

Now add the following configuration file under `packages/senseo_wifi.yaml`:
```yaml
input_boolean:
  senseowifi_brew_normal:
    name: "SenseoWifi Auslöser einfache Tasse brühen"
    initial: off
    icon: mdi:coffee

  senseowifi_brew_double:
    name: "SenseoWifi Auslöser große Tasse brühen"
    initial: off
    icon: mdi:coffee

switch senseowifi:
  - platform: mqtt
    name: SenseoWifi Power
    #
    state_topic: "homie/senseo-wifi-rf21/machine/power"
    state_on: "true"
    state_off: "false"
    #
    command_topic: "homie/senseo-wifi-rf21/machine/power/set"
    payload_on: "true"
    payload_off: "false"
    #
    availability_topic: "homie/senseo-wifi-rf21/$state"
    payload_available: "ready"
    #value_template: "{{ value }}"

sensor senseowifi:
  - platform: mqtt
    name: SenseoWifi Brewed size
    #
    state_topic: "homie/senseo-wifi-rf21/machine/brewedSize"
    #
    availability_topic: "homie/senseo-wifi-rf21/$state"
    payload_available: "ready"
    #value_template: "{{ value }}"

  - platform: mqtt
    name: SenseoWifi OpState
    #
    state_topic: "homie/senseo-wifi-rf21/machine/opState"
    #
    availability_topic: "homie/senseo-wifi-rf21/$state"
    payload_available: "ready"
    #value_template: "{{ value }}"

binary_sensor:
  - platform: mqtt
    name: SenseoWifi Out-of-water
    #
    state_topic: "homie/senseo-wifi-rf21/machine/outOfWater"
    payload_on: "true"
    payload_off: "false"
    #
    availability_topic: "homie/senseo-wifi-rf21/$state"
    payload_available: "ready"
    #value_template: "{{ value }}"

  - platform: mqtt
    name: SenseoWifi Brew
    #
    state_topic: "homie/senseo-wifi-rf21/machine/brew"
    payload_on: "true"
    payload_off: "false"
    #
    availability_topic: "homie/senseo-wifi-rf21/$state"
    payload_available: "ready"
    #value_template: "{{ value }}"

  - platform: mqtt
    name: SenseoWifi Cup available
    #
    state_topic: "homie/senseo-wifi-rf21/machine/cupAvailable"
    payload_on: "true"
    payload_off: "false"
    #
    availability_topic: "homie/senseo-wifi-rf21/$state"
    payload_available: "ready"
    #value_template: "{{ value }}"

  - platform: mqtt
    name: SenseoWifi Cup full
    #
    state_topic: "homie/senseo-wifi-rf21/machine/cupFull"
    payload_on: "true"
    payload_off: "false"
    #
    availability_topic: "homie/senseo-wifi-rf21/$state"
    payload_available: "ready"
    #value_template: "{{ value }}"

automation:
  - id: "1611257531404"
    alias: Regel SenseoWifi Auslöser normale Tasse brühen
    trigger:
      platform: state
      entity_id: input_boolean.senseowifi_brew_normal
      to: "on"
    action:
      - service: mqtt.publish
        data:
          topic: "homie/senseo-wifi-rf21/machine/brew/set"
          payload: "1cup"

  - id: "1611257531405"
    alias: Regel SenseoWifi Auslöser große Tasse brühen
    trigger:
      platform: state
      entity_id: input_boolean.senseowifi_brew_double
      to: "on"
    action:
      - service: mqtt.publish
        data:
          topic: "homie/senseo-wifi-rf21/machine/brew/set"
          payload: "2cup"

  - id: "1611257531406"
    alias: Regel SenseoWifi update beim Ausschalten
    trigger:
      platform: state
      entity_id: binary_sensor.senseowifi_brew
      to: "off"
    action:
      - service: input_boolean.turn_off
        data:
          entity_id: input_boolean.senseowifi_brew_normal
      - service: input_boolean.turn_off
        data:
          entity_id: input_boolean.senseowifi_brew_double

```

Replace "senseo-wifi-rf21" by whatever your machine is called on the MQTT broker.

Hope that helped. Please provide as much info back as you can

Post404, 2021-02-18:
This is excactly what I was looking for. But the Senseo is not responding to power switch or the 1 or 2 cups booleans.
With MQTT explorer I can see that the commands are being received and the states are changing.

I might have to take the Senseo appart again to check if everything is connected right. Or could it be something software sided?

ThomDietrich, 2021-02-19:
Take it one step at a time :)

1. Use `testIO.cpp` to ensure everything works physically, then switch back to the normal firmware mode
2. Observe correct state change etc on the MQTT broker (e.g. OpState should change when you turn the machine on and off) - pay attention to the "debug" MQTT topic for more details. Check this file https://github.com/ThomDietrich/SenseoWifi/blob/master/src/SenseoWifi.cpp for "setProperty" to see what's supposed to be published to MQTT when
4. With confidence that everything works so far, try sending commands via MQTT
5. Only after everything is working set up the connection with Home Assistant. It should work right away

Post404, 2021-02-23:
I used testIO.cpp and it detected that the cup sensor is not present which is correct. Do I need to adjust something in the code for that? Also while in test mode it turned the Senseo On and Off. So at the very least the wires for that are correct.
Then powering it configured and in normal mode makes it beeps twice, so it is connected to wifi and the MQTT broker.
In Supervisor, Mosquitto Broker I see the senseo connection in the log as well.
Then I added the MQTT integration to listen to the topics and be able to manualy publish a packet (is this the same as "send command"?)
When listening to the OpState it doesn't change at all and stays on SENSEO_unknown. It should be SENSEO_NOWATER when turned on.
Debug just says: brew: 19 seconds
Is there something i'm missing?

Post404, 2021-02-24:
I got turning on and off working now from the dashboard! I removed the senseo config and replaced it with yours. Changed the senseo name everywhere, but without translating. The opState is correctly updating and everything else as well. Just the 1 cup and 2 cups switches are not working. Debug says: "no or full cup present. Not executing." I could of course add the sensor, but is there a way to disable this?

ThomDietrich, 2021-02-24:
Great! Congrats! (Btw. be sure to add your voice to #42 😉  )

First of all: The cup sensor is super useful, so think about adding it. Of course, you don't have to. For that reason, I added a flag to disable the use of such a sensor. You must set/unset that flag during the initial setup (the process where you also set wifi password and MQTT credentials). Sorry, you need to reset your machine, there is no way to change the setting now.

Resetting:

* You can send a reset command to the power MQTT topic: https://github.com/ThomDietrich/SenseoWifi/blob/9264955691747e21e436271c5656ed9295bbca57/src/SenseoWifi.cpp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
* Or you can press the reset button for 5 seconds: https://github.com/ThomDietrich/SenseoWifi/blob/9264955691747e21e436271c5656ed9295bbca57/src/SenseoWifi.cpp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

My machines have the reset push button in one of the holes on the bottom of the machine. Quite useful for when you ever need to reconnect it to a new network.

Post404, 2021-02-25:
Might as well just add the sensor and the reset button. It's not that much work at this point. Thanks for helping me out and also making me understand it better!

Post404, 2021-02-28:
Oke, I added the sensor. When in test mode the number is 1024 and changed to ~60 when placing my hand in front of it.
But it is also not detected in both cases, like this:
Testing Cup Detector ... not detected (analog: 1024)
and later:
Testing Cup Detector ... not detected (analog: 59)

I connected the sensor to A0, do I also need to wire it to D0?

Post404, 2021-03-01:
I think I found it out. The sensor i ordered was a TCRT5000 without any board. After checking the versions with the board I noticed that they also have a D0 pin. I'm guessing that if I use that one it will all just work.
So I ordered 2 of those for good measure. Will update when they arive.

Post404, 2021-03-04:
Received the sensor, installed the sensor and now it works perfectly!

Again, thanks for all the help!

ThomDietrich, 2021-03-04:
I played around with the analog input but ended up just going with D0 for simplicity. Too bad you had to order a second time but seems like you got to a happy end. Great!!

I would leave this ticket open as I need to document Home Assistant integration in README.md. Any other details you would suggest adding?

Post404, 2021-03-04:
Now that you mention it, I remember being stuck with the question: "Where exectly do I solder de cables on the senseo board?".
After comparing this: https://github.com/ThomDietrich/SenseoWifi/blob/master/images/DSC09654.jpg picture
with this picture: https://github.com/ThomDietrich/SenseoWifi/blob/master/images/DSC09627.jpg
I eventually got it after a while, but it would have been clearer with a picture like this:
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

ThomDietrich, 2021-10-04:
@Post404 as the buttons and LEDs are in the other side of the PCB, I didn't even think about marking them :D you are of course right...

ThomDietrich, 2021-10-04:
Home Assistant example now in the README. You wouldn't happen to have a cooler configuration by now?

Post404, 2021-10-05:
Yes I do actually, I went full circle. I went back to visualising the Senseo in Homeassistant Lovelace.

You'll need these images in your homeassistant "www" folder: https://we.tl/t-Zrkoq89kdD
It is now set up with a black senseo and a blue cup, but I could easily render different colors.
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

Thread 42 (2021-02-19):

🙋📈 How many active users do we have?

ThomDietrich, 2021-02-19:
Hey all,
for a long time, I was wondering how many people did get inspired by this project and built their own SenseoWifi. This little informal survey is purely voluntary and I'm looking forward to see where we get :)

Please click whichever applies to you:

* 🚀 - My SenseoWifi is up and running
* 🎉 - I did my own additional modifications
* 😕 - I was intrigued but failed to complete the rebuild

If you have a special story to tell, leave a comment.
Thanks all

m4rcu5, 2021-02-19:
:roll_eyes:, not because of the project, but because the plastic parts of my Senseo crumbled when taking it apart. I will take this on when the next machine crosses my path!

ThomDietrich, 2021-02-19:
@m4rcu5 really! I took apart three-four of them and multiple times during development. Maybe yours was old and the parts hard and brittle? If you ever end up buying a new one contact me and I'll send one of the left-over custom PCBs your way!

Post404, 2021-02-25:
Everything in this project has been new for me, ordering the parts, ordering a custom PCB, soldering, dealing with firmware and implementing it with MQTT. But after working on it for a long time and with some help I got it up and running yesterday and i'm very happy with it. I am going to add the cup-detector soon. The joke is that I don't even drink coffee, but my girlfriend is really happy with it. My guess is that it will mostly will be used to turn it on in advance when waking up, I don't think that preparing everything beforehand and then making a cup is going to happen a lot, but this will definitely happen when there are visitors.

It is fun to have these functions now, but the biggest part for me was to learn all the new things and get closer to creating something myself later. For example a motorized roller blind.

muchtkutte, 2021-03-14:
Hallo,

mein ausländisch ist leider sehr miserabel.

Ich habe mir die Platine vor einem halben Jahr zusammen gelötet und in meiner Senseo verbaut. Bei der Gelegenheit habe ich gleich einen Tassenzähler hinzu gefügt welcher aktuell bei 1104 steht. Ganz schön viel Kaffee getrunken. :)

Leider geht bei mir die "Automatik" nicht mehr da mein Tassensensor nichts mehr macht, eventuell ist es neben dem Boiler zu heiß. Ich werde dieser Tage das Gerät nochmals zerlegen und diesen erneuern. Bei der Gelegenheit möchte ich gleich einen Deckelsensor (mir Reedkontakt) verbauen, da ich festgestellt habe das die Senseo auch Kaffee kocht wenn der Pad-Deckel geöffnet ist. Das ist natürlich nicht so schön und mein Bastelwahn sagt das muss geändert werden.

Bei der Gelegenheit mal eine Frage - kann ich den Tassensensor irgendwie über ein MQTT Kommando deaktivieren? Ich habe die Maschine mit meinem Wecker gekoppelt und momentan ist das nicht so schön das ich früh's noch auf die Tassentaste drücken muß. Wasser erhitzen geht zum Glück noch. ;)

ThomDietrich, 2021-03-14:
Hey @muchtkutte,
die Amtssprache auf GitHub ist english aber ich kann dir gern auf Deutsch antworten ;)
Tassenzähler: Toll! Habe ich selbst auch, allerdings auf der anderen Seite von MQTT, also in der Heimautomatisierung bzw in miener InfluxDB.
Mit dem Tassensensor hatte ich nie Probleme. Vielleicht ist deiner willkürlich Opfer eines Fehlers geworden. Ersetze ihn doch einfach mal. Per MQTT umgehen geht leider nicht. Das habe ich nie als Funktion vorgesehen. Solltest du dafür den Code entsprechend erweitern kannst du aber gern einen Pull Request beitragen!
Die Idee mit dem Deckelsensor finde ich SUPER! Wir haben es damals nicht übetreiben wollen und wollten den mechanischen Aufwand gering halten. Wenn du deine Lösung implementiert hast stell doch bitte Aufbau, Code und Fotos uä hier bereit. Vielleicht nehme ich das auch in unseren Aufbauten auf :)

Freue mich über eine ANtwort, um den Thread hier sauber zu halten aber bevorzugt als eingenes Ticket :) Danke!

Vergiss nicht oben die 🚀 und 🎉 als Rekationen hinzuzufügen

Pierre-33, 2021-03-24:
I actually found about this project today, and I totally want to try that :)

I'm new to the electronic part of the project, so it's probably going to be quite a challenge. The end game for me would be to interface it with home assistant, probably through ESPHome. But I might play with your firmware instead, we'll see once I get here :)

I do have questions, though :) It would seem you have a 1.8 version of your pcb but the gerber export doesn't seem to exist for the 1.8. Am I missing something?
For the component parts, I found a PC817X3NSZ9F but it's not clear to me if it's equivalent to the  PC817 you prescribe or if it's a totally different model.

Thanks for this project! :)

Hakzel, 2022-03-27:
I stumbled across this amazing project and I wanted to automate my Senseo as well, even though I am not the coffee drinker in the house ;-)

Do you have a good source for the PCBs? If I try to order them online a quantity of 1 results in prices of 50€ which is a little bit much too handle. I was looking online to find a kit with all the parts but unfortunately without success.

I am also from Germany so any hint into the right direction is highly appreciated :-)

ThomDietrich, 2022-03-28:
Hey @Hakzel, it becomes a lot cheaper if you e.g. order 10 via PCBway or similar. I should still have a few lying around (not the newest version but good enough to succeed). Send me an email and I can mail one to you.

Hakzel, 2022-03-28:
Will do, thanks a lot!

Hakzel, 2022-03-30:
@ThomDietrich thanks for the offer. I already sent you a mail but didn't get any response so far. Any other way to contact you? :-)

ThomDietrich, 2022-03-30:
@Hakzel of course! Let me answer you now ;)

Hakzel, 2022-04-14:
Happy to announce that the SenseoWifi works with the Senseo Quadrante!
Successfully  modded my machine last weekend and it's brewing like a champ now

TonKro, 2023-04-21:
Very interesting project. Can I buy a BCB from someone?

ThomDietrich, 2023-04-21:
@TonKro Baarschot in the Netherlands? Maybe ask here https://github.com/ThomDietrich/SenseoWifi/issues/50

aguiller31, 2025-08-24:
Hey, I just finished modding my Senseo ! Thank you from your amazing work ! Having a full project with PCB, code and a perfect doc with pictures is a blast !! When of my favourite project, nothing to add, it's just perfect !! Thanks again !

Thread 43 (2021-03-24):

It's probably quite the challenge

ThomDietrich, 2021-03-24:
I actually found about this project today, and I totally want to try that :)

I'm new to the electronic part of the project, so it's probably going to be quite a challenge. The end game for me would be to interface it with home assistant, probably through ESPHome. But I might play with your firmware instead, we'll see once I get here :)

I do have questions, though :) It would seem you have a 1.8 version of your pcb but the gerber export doesn't seem to exist for the 1.8. Am I missing something?
For the component parts, I found a PC817X3NSZ9F but it's not clear to me if it's equivalent to the  PC817 you prescribe or if it's a totally different model.

Thanks for this project! :)

_Originally posted by @Pierre-33 in https://github.com/ThomDietrich/SenseoWifi/issues/42#issuecomment-806024204_

ThomDietrich, 2021-03-24:
Hey @Pierre-33

The firmware can already be used with Home Assistant. Find my configuration here: https://github.com/ThomDietrich/SenseoWifi/issues/41
I was also thinking about eventually moving to another framework to be free in which MQTT convention the project communicates with. ESPHome is imho not suited for the project. I'd rather have a lightweight framework tailored to the project. We need a web frontend to configure Wifi and MQTT settings, the rest goes through standard mqtt library. I was looking into something like this: https://github.com/rjwats/esp8266-react

> It would seem you have a 1.8 version of your pcb but the gerber export doesn't seem to exist for the 1.8. Am I missing something?

We did update the PCB over time, however I never had 1.8 produced and hence did never export what I can not verify. You can simply load the project in Fritzing and export to gerber yourself.

> For the component parts, I found a PC817X3NSZ9F but it's not clear to me if it's equivalent to the PC817

As it starts with PC817, yes. The remainder is just details this project does not scratch. Just be sure to get the right form factor ;)

Pierre-33, 2021-03-24:
> We need a web frontend to configure Wifi and MQTT settings
I though the whole point of ESPHome was to take care of that. The wifi configuration seems to be written within the initial firmware and the communication between Home Assistant and the ESP handled without the need of an MQTT server. And as a bonus it seems to support OTA update out of the box.

> We did update the PCB over time, however I never had 1.8 produced and hence did never export what I can not verify. You can simply load the project in Fritzing and export to gerber yourself.
Well, if 1.8 has never been tested, I rather stick with the reliable one :)

> As it starts with PC817, yes. The remainder is just details this project does not scratch. Just be sure to get the right form factor ;)
It does seem to match. I'll probably place my order tomorrow :)

m4rcu5, 2021-03-24:
It is funny that you mention the firmware. I actually stumbled onto this project because I was researching the https://github.com/homieiot/homie-esp8266 project, which is the framework used by this project as well. It served as a really good example for what I was building.
It's a shame the development of the homie-esp8266 project seems to be stalled. I loved the simplicity and MQTT standard it had. I build a module for my air purifier with it :smile:

I felt that ESPHome was a bit to rigid of a framework to build custom devices, which are more then turn thing on/off. But I shall take another look as well.

@ThomDietrich that esp8266-react project looks rather fancy, Though the "react" part scares me away, as front-ends are really not my forte.

ThomDietrich, 2021-03-24:
> Well, if 1.8 has never been tested, I rather stick with the reliable one :)

No don't take that the wrong way. It's the latest version and it would be a shame to work with what is already outdated. I simply did not upload the gerber files. If you are not sure how to do it I can get Fritzing and do it. It's the same effort for me as it is for you :)

> I though the whole point of ESPHome was to take care of that.

ESPHome is great and has its place in the world where you want to connect a few sensors or actors to the outside world. The SenseoWifi project has a complex'ish logic around the state of your Senseo. It does not expose sensors but rather the machine as a functional system. It's simply not the best way to approach this.

The currently used framework homie-esp8266 does it right. It offers a nice web frontend to configure Wifi, MQTT, and further custom settings (like whether you have a cup detector or not) and then facilitates MQTT communication according to the Homie convention.

@m4rcu5 most of the existing logic can stay as it is. I just want to replace Homie by the standard MQTT library and the Home Assistant format, and replace the Homie web frontend by something just as useful. If you know any project that offers that, let me know!

Pierre-33, 2021-03-25:
I never used Fritzing, if it's as simple as clicking the export button, I can probably purchase the software and do it myself, if it's more complicated than that with a lot of export option, I might get lost :)

Ok, I understand the difference between your firmware and ESPHome, my approach was to write all the "intelligence" within homeassistant (using AppDaemon which is so great btw), but I can see the value of your approach. I'll see what I will do once I get there :)

ThomDietrich, 2021-03-25:
Right! They removed the option to download for free! Okay give me 1-2 days and I can export to gerber. How are you going to produce the PCB? There are a few online providers and they massively differ in cost...

Intelligence in home assistant is imho not a good idea, as you need to observe the quickly changing LED. I get your general idea but let me humbly say: As there is already a fully working firmware I wouldn't know why you would go the more efficient way :)

Pierre-33, 2021-03-25:
Thanks, that would be great :) I was thinking about going with aisler.net. They are a bit more expensive than the Chinese companies, but they are in Europe and you order some of the components directly from them. The biggest downside is that you need to order at minium 3 PCBs, but giving my soldering skill, it's probably not such a bad idea to have some spares :)

I'll probably follow your advice regarding the firmware.

Yaad182, 2021-07-11:
I'm thinking of doing this project too, except I have 0 experience with soldering and PCB's, so this'll be interesting... Any tips on where I can buy all these parts including the custom PCB? I live in the Netherlands :)

ThomDietrich, 2021-10-04:
Hey all,
probably too late by now but I have just uploaded the v1.8 gerber export. Hope it's useful for some.

@Yaad182 there are many cheap or fast or convenient options. You can order the PCBs via https://www.pcbway.com and the components should be available on ebay. Can't really give the one best answer here :) Good luck!

Closed 2021-10-04.

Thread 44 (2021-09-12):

error when compiling

bjornmorsman, 2021-09-12:
can somebody help me with my problem?
when i click build in platformio i get this error's

```
> Executing task in folder SenseoWifi-master: C:\Users\Bjorn\.platformio\penv\Scripts\platformio.exe run --environment senseo-wifi <

Processing senseo-wifi (platform: espressif8266; board: d1_mini; framework: arduino)
--------------------------------------------------------------------------------------------------------------------------------------------------------------------------------------------------------------------------------------------------------------------------------------------------------------Verbose mode can be enabled via `-v, --verbose` option
CONFIGURATION: https://docs.platformio.org/page/boards/espressif8266/d1_mini.html
PLATFORM: Espressif 8266 (3.2.0) > WeMos D1 R2 and mini
HARDWARE: ESP8266 80MHz, 80KB RAM, 4MB Flash
PACKAGES:
 - framework-arduinoespressif8266 3.30002.0 (3.0.2)
 - tool-esptool 1.413.0 (4.13)
 - tool-esptoolpy 1.30000.201119 (3.0.0)
 - toolchain-xtensa 2.100300.210717 (10.3.0)
LDF: Library Dependency Finder -> http://bit.ly/configure-pio-ldf
LDF Modes: Finder ~ chain, Compatibility ~ soft
Library Manager: Installing git+https://github.com/homieiot/homie-esp8266.git#cfb3346
FileNotFoundError: [WinError 2] Het systeem kan het opgegeven bestand niet vinden:
  File "C:\Users\Bjorn\.platformio\penv\Lib\site-packages\platformio\builder\main.py", line 177:
    env.SConscript("$BUILD_SCRIPT")
  File "C:\Users\Bjorn\.platformio\packages\tool-scons\scons-local-4.1.0\SCons\Script\SConscript.py", line 591:
    return _SConscript(self.fs, *files, **subst_kw)
  File "C:\Users\Bjorn\.platformio\packages\tool-scons\scons-local-4.1.0\SCons\Script\SConscript.py", line 280:
    exec(compile(scriptdata, scriptname, 'exec'), call_stack[-1].globals)
  File "C:\Users\Bjorn\.platformio\platforms\espressif8266\builder\main.py", line 238:
    target_elf = env.BuildProgram()
  File "C:\Users\Bjorn\.platformio\packages\tool-scons\scons-local-4.1.0\SCons\Util.py", line 658:
    return self.method(*nargs, **kwargs)
  File "C:\Users\Bjorn\.platformio\penv\Lib\site-packages\platformio\builder\tools\platformio.py", line 62:
    env.ProcessProjectDeps()
  File "C:\Users\Bjorn\.platformio\packages\tool-scons\scons-local-4.1.0\SCons\Util.py", line 658:
    return self.method(*nargs, **kwargs)
  File "C:\Users\Bjorn\.platformio\penv\Lib\site-packages\platformio\builder\tools\platformio.py", line 140:
    project_lib_builder = env.ConfigureProjectLibBuilder()
  File "C:\Users\Bjorn\.platformio\packages\tool-scons\scons-local-4.1.0\SCons\Util.py", line 658:
    return self.method(*nargs, **kwargs)
  File "C:\Users\Bjorn\.platformio\penv\Lib\site-packages\platformio\builder\tools\piolib.py", line 1062:
    project.install_dependencies()
  File "C:\Users\Bjorn\.platformio\penv\Lib\site-packages\platformio\builder\tools\piolib.py", line 898:
    lm.install(spec)
  File "C:\Users\Bjorn\.platformio\penv\lib\site-packages\platformio\package\manager\_install.py", line 48:
    pkg = self._install(
  File "C:\Users\Bjorn\.platformio\penv\lib\site-packages\platformio\package\manager\library.py", line 81:
    return super(LibraryPackageManager, self)._install(
  File "C:\Users\Bjorn\.platformio\penv\lib\site-packages\platformio\package\manager\_install.py", line 97:
    pkg = self.install_from_url(spec.url, spec, silent=silent)
  File "C:\Users\Bjorn\.platformio\penv\lib\site-packages\platformio\package\manager\_install.py", line 141:
    vcs = VCSClientFactory.new(tmp_dir, url)
  File "C:\Users\Bjorn\.platformio\penv\lib\site-packages\platformio\package\vcsclient.py", line 54:
    obj = getattr(sys.modules[__name__], "%sClient" % type_.title())(
  File "C:\Users\Bjorn\.platformio\penv\lib\site-packages\platformio\package\vcsclient.py", line 137:
    self.configure()
  File "C:\Users\Bjorn\.platformio\penv\lib\site-packages\platformio\package\vcsclient.py", line 146:
    result = proc.exec_command([cls.command, "--exec-path"])
  File "C:\Users\Bjorn\.platformio\penv\lib\site-packages\platformio\proc.py", line 117:
    p = subprocess.Popen(*args, **kwargs)
  File "C:\Users\Bjorn\.platformio\python3\lib\subprocess.py", line 951:
    self._execute_child(args, executable, preexec_fn, close_fds,
  File "C:\Users\Bjorn\.platformio\python3\lib\subprocess.py", line 1420:
    hp, ht, pid, tid = _winapi.CreateProcess(executable, args,
========================================================================================================================================= [FAILED] Took 0.85 seconds =========================================================================================================================================The terminal process "C:\Users\Bjorn\.platformio\penv\Scripts\platformio.exe 'run', '--environment', 'senseo-wifi'" terminated with exit code: 1.

Terminal will be reused by tasks, press any key to close it.
```

ThomDietrich, 2021-10-04:
Hey,
I can't help with the issue but I can confirm that I was able to compile and flash the firmware just now. You might want to clean your environment. I recon this is a PlatformIO error, not an error with this project. Please let me know if you got it working!

Closed 2021-10-04.

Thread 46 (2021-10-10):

Cup Full Logic

Post404, 2021-10-10:
Now that I added the full cup reminder automation I noticed that the full cup state isn't correct all the time.
I think the currect logic (correct me if i'm wrong) is that "Full cup" sets to true when brewing is done.
And "Full cup" goes to false when the cup is removed.
The logic for the brewing state is that it sets the state to brewing when brewing is started, waits untill heating is done and then changes state to ready.
If this is correct this means that if you remove the cup before brewing is finished (which happens almost every time), that the full cup status change will happen after removing the cup. That way there won't be a trigger to change that back to empty because the cup is allready gone.

I think it would be more usefull to set cup full to true when brewing is started, but only when there is a cup available, that way there is allways a cup to remove and set the state back to cup empty again.

ThomDietrich, 2021-10-10:
Crazy! I never caught that :)

Your guess is right. This line sets the cup to be "full" after brewing, even though you could have taken the cup away in-between.

https://github.com/ThomDietrich/SenseoWifi/blob/bfe35350e810160e3195d59e1d38f4b9a968df4c/src/SenseoWifi.cpp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

I don't like moving the line to the beginning of the brew process. After all, it's not logical to claim the cup is full when it's certainly not ;)

I think one step to the solution is rather easy. We simply have to re-check whether a cup is actually available:

```
if (CupDetectorAvailableSetting.get() && myCup.isAvailable()) myCup.fillUp();
```

However, this doesn't solve the whole issue as you could have removed the cup in-between and added a new one right away... feels like we need a piece of additional logic to `mycup`, so that it is aware of it currently being filled.

1. At beginning of the bew: Set `mycup.beingFilledUp()`
2. After the brew: Call `mycup.fillUp()` only of `mycup.isBeingFilledUp()`
3. When `mycup.cupAvailable` changes at any point, set the variable `mycup.beingFilledUp` to false

That should capture all cases I can think of. Let me know what you think.

Post404, 2021-10-18:
I duplicated you automations to be able to automatically brew 1 cup and 2 cups.
I just tested the 1 cup automation and it didn't work.
It has to do with something a noticed earlier.
This is what happens on my end: Turn on Senseo > heating state > very shortly the brewing state> Ready state
That means that after heating, step 3 is triggered before step 2. So it is turned off before doing anything.
I changed the trigger of step 3 to this to fix is:
```
    trigger:
      platform: state
      entity_id: sensor.senseowifi_opstate
      from: "SENSEO_BREWING"
      for:
        hours: 0
        minutes: 0
        seconds: 0
        milliseconds: 500
```

I only tested this once but I thing 500 milliseconds should be more then enough.

ThomDietrich, 2021-10-18:
Hey!
Great catch. I am not with my machine in the next few days and can't test. The trigger is "from: SENSEO_BREWING" - sounds like Home Assistant sees a state change that really shouldn't be there...
Imho we want this either fixed in the firmware or by doing something like:

```
      from: "SENSEO_BREWING"
      to:
        - "SENSEO_READY"
        - "SENSEO_NOWATER"
        - "SENSEO_OFF"
```
Seems overkill.
Could you capture every state change an see where this comes from? My approach would be to subscribe to the opstate topic with any MQTT client. If there is indeed a non-sensical state message, it should be removed from the firmware.

ThomDietrich, 2021-11-04:
Hey, something still doesn't seem right:

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

I am back home now and will explore where this could possibly come from. Best!

ThomDietrich, 2021-11-04:
Silly me, it turned out to be exactly what you described in your second comment... which I read after going on a bug hunt myself :) I agree with your logic. I've changed the code to not fill a non existing cup, even when triggered manually on the machine. If the microcontroller doesn't know about a cup, it doesn't make sense to assume a filled cup.

----

Regarding your issue, I did take a look at how my machine behaves, but even after multiple tries I get a pretty clean picture, e.g.

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

I wonder if your LED timing is a bit different?

Post404, 2021-11-06:
Thanks for all this!
My Senseo is just less powerful then.
It takes 1 min 21 sec to heat up.

i will also try out the changed automations.

ThomDietrich, 2021-11-06:
I ran into another weird behavior just now:
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
After leaving the machine in READY this happened after a while. Confused by the constant beeping I turned it off. I suspect this is related to the reheating that happens after a while.

ThomDietrich, 2021-11-06:
About the reheating behavior. I didn't encounter it again. However, I also realized that I don't want the machine to even wait that long in the ready state. I've added a rule to turn the machine off after 10 minutes in SENSEO_READY. You can see that in the last block here:

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

Post404, 2021-11-09:
I think I see what is happening here. Your Senseo never really cools down because you are drinking so much coffee!
My Senseo is not in a cold place at all. It would take even longer if that was the case.
I've never used the brew-directly-after-heating logic, at least not knowingly by holding down the button.
If the only side effects is that it takes longer before it realises that it is brewing? If that is the case then I don't see a problem.

ThomDietrich, 2021-11-14:
Hey @Post404 , I've just pushed updated numbers that should work for you and myself. Best!

Btw. the only issue is that the brew-directly-after-heating logic might detect the wrong coffee size now. Well well 🤷‍♂️

Post404, 2021-11-14:
Thanks, I will apply the update! I think this can be closed

ThomDietrich, 2021-11-16:
Still not 100% avoided 🤔 I did not expect this too be such a complicated issue ^^

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

Closed 2021-11-14.

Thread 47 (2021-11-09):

OTA update

Post404, 2021-11-09:
I've tried a few times to update OTA, but I never got it to work. What am I missing here?
In Visual Studio Code I changed the ip, username, password and the senseo name in de platformio.ini file.
added "upload_port = 192.168.xx.xx"
added "build_dir = mybuildfiles"
changed the file location from "$BUILD_DIR/firmware.bin" to ".pio/build/senseo-wifi/firmware.bin"
Uploading goes a long way and seems to work for the most part but ends with:
```
Traceback (most recent call last):
  File "D:\Projecten\Home Assistant\Wifi Senseo\SenseoWifi-master 9 nov\SenseoWifi-master\ota_updater_202011.py", line 4, in <module>
    import paho.mqtt.client as mqtt
ModuleNotFoundError: No module named 'paho'
*** [upload] Error 1
```

ThomDietrich, 2021-11-09:
Hey!
Uploading directly through PlatformIO doesn't work. That's out of the box only possible via USB, not OTA.

First of all, try from a normal command line. The command is given here: https://github.com/ThomDietrich/SenseoWifi#ota-updates (you can use the command line inside VSCode, if the error from above pops up you need to execute once `pip3 install paho-mqtt`.

After you got the command working I did actually implement the change to make all of this work right out of PlatformIO two days ago: https://github.com/ThomDietrich/SenseoWifi/blob/b9e0cf8c536b316d8d3fe9397ac7d7e5beb8d335/platformio.ini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 (you need to change the details to your setup)

Post404, 2021-11-09:
Everytime I updated I tried to get OTA working and then not get it to work and shamefully dissasemble it again.

Allright I'm trying the command through terminal now. What I did wrong is that I used the IP of the Senseo and not of Home Assistant and I had to change python3 to py. So that is fixed now.
When using the command in VScode it is saying that the device is already up to date. Perfect!
So from now on I can just download updated files, replace them and use the command again to update.
Without having to dissasemble the thing over and over.

Is there an easy way to pull the latest files?

I did also updated the upload_command in platformio.ini.
When using the task button "Upload" or "Upload Filesystem Image OTA" it's still saying it is missing paho.
I allready installed that (version 1.5.1).

ThomDietrich, 2021-11-09:
The devil is in the details, can't say for sure but hope you get it working.

The important thing, upload via command line seems to be working, so that's amazing.

> Is there an easy way to pull the changed files?

Yes generally you should go with git. if you have no experience with it look at any online tutorial, it has some kinks to know about but is super useful. In short: you can always quickly `git pull` the latest changes (VSCode has support for that), then press "Build", then upload through command line. Voila!

As I said, please share either a PR or simply your thoughts about what needs to be improved in the README and I can take care of it.

Post404, 2021-11-14:
Thanks for the tip, I will look into this.
The only thing that might clear things up for beginners like me is that the command is easiest used in VScode.
And that it works by connecting to de MQTT broker. I was thinking it was directly somehow.

For now I'm trying to update with the command in VScode and it is saying it is already up to date with md5 checksum and then some long string of numbers and letters.
It's on 1.7.3, is this the latest one?

ThomDietrich, 2021-11-14:
Nope :)

https://github.com/ThomDietrich/SenseoWifi/blob/129a7b1b5c5ec63c72e101dc2d3d28da20b56185/src/SenseoWifi.cpp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

I might add a few sentences around the command inside the README

Post404, 2021-11-14:
Thanks! I got it working, I didn't do anything different, but I guess i'm a wizard.

Closed 2021-12-23.

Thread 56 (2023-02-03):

Second try :)

Pierre-33, 2023-02-03:
Hey! I'm back :) After almost 2 years, I wan't to give it another try. Printing the pcb online was a bit daunting so I want to give it a try with a protoboard. I do have a few questions though (forgive me for the dumb one)

- what are the resistor for? Can't you just connect the side of the octocoupler that emit light directly to an out pin of the ESP?
- I understand from the schematic what side of the octocoupler should be connected toward the esp and which should be toward the senseo, but I have no idea how to know what is what from the actual piece of hardware. Is there any convention to know which part emit light and which part receive them?
- I ordered a HLK-PM01, but it seems tricky to use. I dig a bit on the internet and it seems to involve using fuse (https://randomnerdtutorials.com/esp8266-hi-link-hlk-pm03/) and I'm not very confortable soldering a custom pcb for 220v (and it seems the pin of the HLK doesn't want to fit into any of my protoboard anyway). Can you update the reference of the step down converter you use? (the link on ebay is broken)

The last things is more of a suggestion. Have you considered to hack directly the buttons into the esp to add nice behavior like
- Pressing the cup button could trigger the full brewing cycle. (turn on, wait for warm up, brewing, turn off)
- A long press of the cup button could turn on an mqtt switch that would be used by home assistant (or your favorite automation) to program a coffee for the next morning
- A long press of the main button could reset your firmware (no need for an extra button)
- Requesting a coffee with no cup present could be rejected and trigger a sound from the buzzer

ThomDietrich, 2023-02-03:
Hey!
I will respond to everything later today. Just a quick question though: Where do you live? I could send a letter with one of my spare PCBs your way.

Pierre-33, 2023-02-03:
Thanks, that would be nice :) I live in France.
But depending on your answer on the second part of my message, I might want to try the improvement I propose. I could contribute to the c++ implementation with a little help on the electronic part (mostly where to put resistor)

Pierre-33, 2023-02-05:
A little update on my side. I did some reading this week-end and now I know how to read the octocoupler pinout and manage to use one for another simpler project. I did find out as well that without the resistor the octocoupler burn, so the resistor must be useful :) I just don't know how to calculate the needed value yet, so I just use the same as you.

ThomDietrich, 2023-02-06:
Hey!

Jup that pretty much answers it. Looking at the [datasheet](https://global.sharp/products/device/lineup/data/pdf/datasheet/PC817XxNSZ1B_e.pdf) we learn that pin 1 is marked by a shiny dot on the top of the chip ("Anode mark"). On my PCB it is marked by a rectangular pad. The resistor follows the standard rules for an in-series resistor for an LED. Seems like I went with a bigger resistor, which in this case does not hurt and is often good practice.
Try yourself (3.3V, 1.2V. 5..20mA): https://www.digikey.de/en/resources/conversion-calculators/conversion-calculator-led-series-resistor

Am I correct to assume that you are on a beginner level in electrical engineering?

> I'm not very comfortable soldering a custom PCB for 220v

And you definitely shouldn't! Please buy a ready to be used component as I did, or permanently power the D1 Mini with a separate USB power supply.
This is my solution: https://raw.githubusercontent.com/ThomDietrich/SenseoWifi/master/images/DSC09646.jpg (no own soldering on the 230V side) https://www.ebay.de/itm/232569563115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

> Have you considered to hack the buttons directly into the ESP to add nice behavior like

I did consider this a couple of times. We didn't feel the additional components and effort were justified. It's certainly possible to disconnect the buttons from the Senseo and directly to the ESP GPIO pins. One blocker today: The D1 Mini does not have enough GPIOs free to connect three buttons.
In the beginning we didn't want to break default behavior of the machine, later we realized it wasn't needed. I still mostly handle it by hand, eventually we use Alexa or an Ikea Zigbee button and Home Assistant to start a complete brewing cycle.
I find your suggestion intriguing and would consider it for a new project, here and today I don't see the need.

Happy to send over a PCB if you carry the postal service fee.

Pierre-33, 2023-02-06:
> Am I correct to assume that you are on a beginner level in electrical engineering?

Yes, you are totally right :) I purchased a book recently and having a lot of fun! Hopefully, I should be soon able to calculate the right resistor value myself :)

> This is my solution: https://raw.githubusercontent.com/ThomDietrich/SenseoWifi/master/images/DSC09646.jpg (no own soldering on the 230V side) https://www.ebay.de/itm/232569563115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

I assumed the red wire on your picture are the 220v one, right? So you still have to solder your own cable (obviously bigger section) to the step-down PCB? Is that safe? I feel like the part where the red wire meet the step-down PCB is totally unprotected.
I find this one which seems quite similar : https://www.amazon.fr/AC-DC-700mA-Power-Supply-Module/dp/B08KH82YK1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 but I don't understand why there is 3 output pin. Vc++, GND - and a mysterious output. Does yours as that?

On that same topic, if I understood correctly it's safe to have the ESP connected to the computer with the USB cable AND the Senseo operating on 220v at the same time? (Of course the Senseo cover should be put back in place or extra caution should be taken not to touch anything inside while it's powered on).

> The D1 Mini does not have enough GPIOs free to connect three buttons.
Oh, I didn't think about that :-/ I didn't open my Senseo yet, how much space do we have inside? Do you think a full-size esp 8266 would fit in or did you pick the mini because of the tight space?

> Happy to send over a PCB if you carry the postal service fee.
I'll see how it goes with my test and I might ask you for one when I'm ready, thanks for offering.

ThomDietrich, 2023-02-06:
> I purchased a book recently and having a lot of fun! Hopefully, I should be soon able to calculate the right resistor value myself :)

This is great. Carry on! 🎉

> I assumed the red wire on your picture are the 220v one, right?

As you can see, I used T-tap connectors on the wire side: https://www.amazon.fr/120-pi%C3%A8ces-Connecteurs-%C3%A9lectriques-tap/dp/B077YB123S However, you might be right, the red wires are soldered on the PCB side. In this case it is totally fine: The consumption of the additional electronics is minimal, so is the power over the AC input of the power supply.

No need to be scared by these steps, but cautious. Keep the machine disconnected; install T-taps and ensure proper soldering results; feed 5V wires out of the machine for testing; ensure that the power supply is properly fixed and protected inside the Senseo (I suggest to hot glue to the floor). Only after everything is installed and sealed away start your first testing and measure that stable 5V are supplied.

As before: Do not connect AC power (Senseo and/or AD-DC power supply) and USB at the same time. This is first and foremost a safety precaution. The Senseo is not properly AC separated. Somewhere between the Senseo electronics, the AC-DC power supply and your laptop/PC you might encounter voltage/potential differences which can give you a scare, damage your ESP, or your Laptops USB port.

> Vc++, GND - and a mysterious output

Not sure what that is but the component looks okay otherwise

> Oh, I didn't think about that :-/ I didn't open my Senseo yet, how much space do we have inside?

If you really wanted to make this happen, you could work with pin A0, which is not actually used in conjunction with the TCRT5000. This looks like a nice explanation: https://electrocredible.com/multiple-buttons-on-one-analog-pin-arduino-adc
The inside is not spacious but you would probably be able to add a bigger microcontroller. Beware that the ESP8266 only offers up to 11 GPIOs and this project here does only support the ESP8266.

Pierre-33, 2023-02-06:
> However, you might be right, the red wires are soldered on the PCB side. In this case it is totally fine: The consumption of the additional electronics is minimal, so is the power over the AC input of the power supply.
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
Pierre-33, 2023-03-09:
A lot of progress has been made since my last post :)

I prototyped the voltage divider to read all the buttons with A0, it turns out to be more complicated than expected because the switch share their ground wire with the LED but I managed to make it work and I intend to put that part of the circuit in the little PCB on my picture which might make it compatible with your PCB. As a nice addition, I gain control over the Senseo Led which allow me to handle custom blinking patterns that actually match the esp state machine. Now brewing is 2s on and 200ms off.

I find out that not all Senseo are born equal. Mine doesn't have the feature that turn-on, warm up brew and turn off when you press the cup button. Well... it was before I took control over the input button :) Now it's handled by the esp firmware!

Most of my weird behavior was caused by me sending command to senseo esp via MQTT while the Senseo wasn't plugged and then plugging it afterwards. It seems the FSM was totally desync after that. It shouldn't happen during normal operation and it is only possible because it's powered on USB for now.

So what next for me?

- Rewrite the FSM with the new buttons . I should be able to do something more robust as I don't have to guess from the LED state if I'm in brewing or heating
- Holding the power button will beep 3 times and then reset the machine
- Pressing cup button will trigger a full brewing cycle (almost done, I just have to find out why it doesn't turn off the machine)
- Pressing cup button without a cup will trigger an error beep instead of brewing (or maybe a specific led pattern)
- Holding cup button will raise a binary_sensor in Home Assistant that will in return trigger a coffee for the next morning when I woke up. I will probably use a very slow blinking pattern when a coffee is pending (like once a minute).

I feel like doing something stupid like turn off the light of my kitchen when I press two buttons of my Senseo, just for the fun of it. But unfortunately the voltage divider doesn't give me different reading if I press more than one switch at the same time, if you have any tricks left in your bag concerning that, I'm interested :)

ThomDietrich, 2023-03-09:
Wow that's great progress! Congrats!!
I am happy with my old Senseo as it works today and won't apply thee changes. However, maybe I could with the new machine. :D

Voltage divider: It is possible to detect more than one button in parallel. The theory is that you can dimension your circuit to generate something like a binary encoding:

* Button 1 pressed: Value=1
* Button 2 pressed: Value=2
* Button 3 pressed: Value=4
* Button 4 pressed: Value=8

* Value=5 --> Buttons 1 and 3 pressed

The problem with this is the margin of error! You should open Excel and play around with some combinations of resistors to see how you might keep all relevant values reasonably apart from each other. Google for "resistor ladder binary" to learn more: https://www.best-microcontroller-projects.com/R-2R-ladder.html

Pierre-33, 2023-03-09:
Bitfield with resistor!! :) Once again it's exactly what I was looking for, thanks a lot!

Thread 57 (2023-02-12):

Replace TCRT5000?

luftpumpe83, 2023-02-12:
Hi!
Just found your project and it's really amazing.
Will order some PCBs right now.
But one question: is it possible to replace the TCRT5000 with another sensor? I'd really like to use the cup detection, but don't want to cut a hole in the Senseo's housing.
Best regards,
Oliver

ThomDietrich, 2023-02-13:
Hey Oliver,
certainly understandable and a valid question we asked ourselves as well.

Short answer: No.

Long answer: The TCRT is the best option I am aware of. I would refrain from any sensor under the cup (push button or pressure sensor) for the obvious reasons around moisture and cleaning. A contactless sensor is the way to go. An alternative might be an ultrasonic sensor or any other radio sensor, which might work behind the plastic - however, a probable issue is the limited space inside the machine. Be my guest to give it a try.

Honestly, in my humble opinion, don't bother. The small hole in the housing is barely visible and no one ever realized and asked about it. On the contrary, it was always convenient for me to say "yeah I've hacked the coffee machine, check out this sensor for cup detection!"

Pierre-33, 2023-02-20:
For your information, I plan to try this one very soon: https://www.az-delivery.de/en/products/ir-abstand-sensor-modul
It seems to be pretty much the same but with a different form factor. I hope to achieve something cleaner with two round holes for the leds than a clumsy rectangle (and I should be able to bend the led a bit if the space between the hole is not perfectly right.

I'll let you know how it goes, but I don't expect to be at the drilling stage before a few weeks.

ThomDietrich, 2023-02-20:
Good idea. From the far my modification looks like a clean little rectangular element, as if it belongs to the machine design. Btw "from the far": because of the nozzle, you can't even see it when next to the machine. As said before: Don't bother :)

Pierre-33, 2023-02-25:
I received the  distance sensor I mentioned before and it works exactly like the TCRT5000 you use but it's way bigger (basically the size of two LEDs). Turn out the TCRT5000 is way smaller than I imagined. No sure which one I'm going to actually use within my Senseo.

luftpumpe83, 2023-02-26:
Okay... will think about it... Thank you :)

ThomDietrich, 2023-03-09:
Nice! Looks great
Btw which Senseo is that? Feel free to add it as supported to the Readme

luftpumpe83, 2023-03-09:
It's Senseo Quadrante HD 7863/60 from 2013.
I've just uploaded the file to Thingiverse. For the Quadrante it's easy because the surface is even. The "normal" Senseos have a curved housing, so you have to know its radius to create a similar holder.

I just created an automatisation to let it beep "tone3" if the cup is recognized and "tone4" if it's no longer recognized :)
It's because if you put the cup too close to the sensor, it will not be recognized. Tried to adjust the sensor but that behaviour didn't change, so I had to add a little audio feedback.
Is it possible to have a tone sequence for the buzzer? Tried to publish one tone after the other via MQTT but it seems you can only publish one value per payload.

ThomDietrich, 2023-03-09:
I must admit that the buzzer handling is a bit of a weak spot of the code as it is today. `tone()` is a blocking method, which could theoretically fail other actions of the machine.

I have recently hacked together a better solution, which you might like. It utilized ezBuzzer instead of tone. Would you like to give this a try? I would appreciate a PR that replaces all `tone()` calls by ezbuzzer.

```cpp
/*
SenseoWifi.cpp - base file for the SenseoWifi project.
Created by Thomas Dietrich, 2016-03-05.
Released under some license.
*/

#include "SenseoLed.h"
#include "SenseoSM.h"
#include "pins.h"
#include "constants.h"
#include <ezBuzzer.h>

SenseoLed mySenseoLed(ocSenseLedPin);
SenseoSM mySenseoSM;
ezBuzzer buzzer(beeperPin);

int melody1[] = {
  NOTE_C7
};
int noteDurations1[] = {
  2
};

int melody2[] = {
  NOTE_E5, NOTE_E5, NOTE_F5, NOTE_C5
};
int noteDurations2[] = {
  4, 8, 8, 2
};

int melody3[] = {
  NOTE_C4, NOTE_C5
};
int noteDurations3[] = {
  4, 8
};

/**
* Called by the LED changed interrupt
*/
//void ICACHE_RAM_ATTR ledChangedHandler() {
void IRAM_ATTR ledChangedHandler() {
  mySenseoLed.pinStateToggled();
}

/**
* Senseo state machine, transition reaction: exit actions
*/
void senseoStateExitAction() {
  switch (mySenseoSM.getStatePrev()) {
    case SENSEO_OFF: {
      int length = sizeof(noteDurations3) / sizeof(int);
      buzzer.playMelody(melody3, noteDurations3, length);
      break;
    }
  }
}

/**
* Senseo state machine, transition reaction: entry actions
*/
void senseoStateEntryAction() {
  switch (mySenseoSM.getState()) {
    case SENSEO_OFF: {
      break;
    }
    case SENSEO_HEATING: {
      break;
    }
    case SENSEO_READY: {
      //tone(beeperPin, 1536, 500);
      int length = sizeof(noteDurations1) / sizeof(int);
      buzzer.playMelody(melody1, noteDurations1, length);
      break;
    }
    case SENSEO_BREWING: {
      break;
    }
    case SENSEO_NOWATER: {
      //tone(beeperPin, 4096, 1800);
      int length = sizeof(noteDurations2) / sizeof(int);
      buzzer.playMelody(melody2, noteDurations2, length);
      break;
    }
    case SENSEO_unknown: {
      break;
    }
  }
}

void setup() {
  //Serial.begin(115200);

  pinMode(ocPressLeftPin, OUTPUT);
  pinMode(ocPressRightPin, OUTPUT);
  pinMode(ocPressPowerPin, OUTPUT);
  pinMode(ocSenseLedPin, INPUT_PULLUP);

  digitalWrite(ocPressPowerPin, LOW);
  digitalWrite(ocPressLeftPin, LOW);
  digitalWrite(ocPressRightPin, LOW);

  //pinMode(beeperPin, OUTPUT);
  pinMode(resetButtonPin, INPUT_PULLUP);
  pinMode(cupDetectorPin, INPUT_PULLUP);
  pinMode(cupDetectorAnalogPin, INPUT);

  attachInterrupt(digitalPinToInterrupt(ocSenseLedPin), ledChangedHandler, CHANGE);
  tone(beeperPin, 1536, 2000);
  delay(2500);
}

void loop() {
  buzzer.loop();
  mySenseoLed.updateState();
  mySenseoSM.updateState(mySenseoLed.getState());
  if (mySenseoSM.stateHasChanged()) {
    senseoStateExitAction();
    senseoStateEntryAction();
  }
}

```

Pierre-33, 2023-03-09:
Grab the latest from my fork : https://github.com/Pierre-33/SenseoWifi
You should be able to request "melody1", "melody2" and "melody3" from MQTT now in addition to the previous tone. I couldn't test it myself but it does compile so it's a great start :)

You can then try to add yourself more melody in the buzz function.

luftpumpe83, 2023-03-09:
Working! Thank you! Now I will find out how to use it and become a composer ;)
(btw: deleted senseo_wifi.yaml as you said in my other issue and it's still working)

Pierre-33, 2023-03-09:
Let me know if you came up with some nice tune and I’ll them to my pull request.

ThomDietrich, 2023-03-09:
@Pierre-33 looks perfect! Because of the blocking method issue I would ideally get rid of `tone()` all together. Let's discuss in a PR?

Pierre-33, 2023-03-10:
The thing is that I don't know how to submit a PR with only the buzz change (I'm  not so much confortable with git, I'm more of a peforce guy myself). So I was waiting for you to accept the one with HomeAssistant discovery before opening the one with the buzzer.

Pierre-33, 2023-05-21:
@luftpumpe83 how is going your Senseo? I'm affraid that by using AsyncMqttClient 0.9.0 in my fork I introduced an issue. Your Senseo won't be able to reconnect to the MQTT server if your wifi connection drop for a while.

This can be fix with by adding this dirty hack on the HomieEventType::WIFI_CONNECTED events:

```c++
void onHomieEvent(const HomieEvent &event)
{
    switch (event.type)
    {
    case HomieEventType::WIFI_CONNECTED:
        // If myIP is set, this is not the first time the wifi is connected
        if (myIP != IPAddress(0,0,0,0))
        {
            // With AsyncMqttClient 0.9.0, Homie can't reconnect to MQTT after a wifi disconnection
            // Unfortunately 0.8.2 (which is the version packaged with Homie), has a mqtt max payload size to low for sending Home Assistant Autodiscovery config
            // This is clearly a bad workaround but I have nothing better yet
            Serial.println("We lost Wifi Connection during Operation. The Esp need to reboot");
            Homie.reboot();
        }
        myIP = event.ip;
        ...
        break;
    ...
    }
}
```

You'll need to declare your variable somewhere in your SenseoWifi.cpp as well

```c++
...
HomieNode senseoNode("machine", "senseo-wifi", "senseo-wifi");
IPAddress myIP = IPAddress(0,0,0,0);
...
```

luftpumpe83, 2023-06-29:
Hi,
it's still working fine. But as you say, sometimes the connection is lost. So I will try your "dirty hack" soon :)

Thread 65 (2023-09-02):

Upload Problem

mrhary, 2023-09-02:
hecking size .pio/build/d1_mini/firmware.elf
Advanced Memory Usage is available via "PlatformIO Home > Project Inspect"
RAM:   [======    ]  55.2% (used 45212 bytes from 81920 bytes)
Flash: [======    ]  59.0% (used 616180 bytes from 1044464 bytes)
Building .pio/build/d1_mini/firmware.bin
Creating BIN file ".pio/build/d1_mini/firmware.bin" using "/home/harald/.platformio/packages/framework-arduinoespressif8266@3.30101.0/bootloaders/eboot/eboot.elf" and ".pio/build/d1_mini/firmware.elf"
Configuring upload protocol...
AVAILABLE: espota, esptool
CURRENT: upload_protocol = esptool
Looking for upload port...
Using manually specified: /dev/ttyUSB1
Uploading .pio/build/d1_mini/firmware.bin
usage: esptool [-h] [--chip {auto,esp8266,esp32,esp32s2,esp32s3beta2,esp32c3}]
               [--port PORT] [--baud BAUD]
               [--before {default_reset,no_reset,no_reset_no_sync}]
               [--after {hard_reset,soft_reset,no_reset}] [--no-stub]
               [--trace] [--override-vddsdio [{1.8V,1.9V,OFF}]]
               [--connect-attempts CONNECT_ATTEMPTS]
               {load_ram,dump_mem,read_mem,write_mem,write_flash,run,image_info,make_image,elf2image,read_mac,chip_id,flash_id,read_flash_status,write_flash_status,read_flash,verify_flash,erase_flash,erase_region,version,get_security_info}
               ...
esptool: error: unrecognized arguments: --auth=senseo
*** [upload] Error 2
======================================== [FAILED] Took 113.80 seconds ========================================

 *  The terminal process "platformio 'run', '--target', 'upload'" terminated with exit code: 1.
 *  Terminal will be reused by tasks, press any key to close it.

Wenn ich das Upload_Flags deaktiviere läuft es durch, jedoch komm ich trotzdem nicht auf die Settings.html

ThomDietrich, 2023-09-05:
Hallo @mrhary,
hast du das Problem lösen können? Eine Fehlerursache die man dokumentieren sollte?

Closed 2023-09-05.

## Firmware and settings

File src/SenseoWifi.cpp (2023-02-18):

/*
SenseoWifi.cpp - base file for the SenseoWifi project.
Created by Thomas Dietrich, 2016-03-05.
Released under some license.
*/

#include <Homie.h>

#include "SenseoLed.h"
#include "SenseoSM.h"
#include "SenseoControl.h"
#include "Cup.h"
#include "pins.h"
#include "constants.h"
#include "testIO.cpp"

SenseoLed mySenseoLed(ocSenseLedPin);
SenseoSM mySenseoSM;
SenseoControl myControl(ocPressPowerPin, ocPressLeftPin, ocPressRightPin);
Cup myCup(cupDetectorPin);

HomieNode senseoNode("machine", "senseo-wifi", "senseo-wifi");
HomieSetting<bool> CupDetectorAvailableSetting("cupdetector", "Enable cup detection (TCRT5000)");
HomieSetting<bool> BuzzerSetting("buzzer", "Enable buzzer sounds (no water, cup finished, ...)");

/**
* Called by the LED changed interrupt
*/
void ICACHE_RAM_ATTR ledChangedHandler() {
  mySenseoLed.pinStateToggled();
}

/**
* Called by Homie upon an MQTT message to '.../power'
* MQTT response is sent from this routine, as pessimistic feedback from state machine is too slow and triggers a timeout in e.g. Home Assistant.
*/
bool powerHandler(const HomieRange& range, const String& value) {
  if (value != "true" && value !="false" && value != "reset") {
    senseoNode.setProperty("debug").send("power: malformed message content. Allowed: [true,false,reset].");
    return false;
  }

  if (value == "true" && mySenseoSM.getState() == SENSEO_OFF) {
    myControl.pressPowerButton();
    senseoNode.setProperty("power").send("true");
  }
  else if (value == "false" && mySenseoSM.getState() != SENSEO_OFF) {
    myControl.pressPowerButton();
    senseoNode.setProperty("power").send("false");
  }
  else if (value == "reset") {
    senseoNode.setProperty("power").send("false");
    tone(beeperPin, 4096, 8000);
    Homie.reset();
  }
  return true;
}

/**
* Called by Homie upon an MQTT message to '.../brew'.
* No MQTT response is sent from this routine, as pessimistic feedback will be handled in the state machine.
*/
bool brewHandler(const HomieRange& range, const String& value) {
  if (value != "1cup" && value !="2cup" && value !="descale") {
    senseoNode.setProperty("debug").send("brew: malformed message content. Allowed: [1cup,2cup,descale].");
    return false;
  }

  if (CupDetectorAvailableSetting.get()) {
    if (myCup.isNotAvailable() || myCup.isFull()) {
      senseoNode.setProperty("debug").send("brew: no or full cup present. Not executing.");
      return false;
    }
  }

  if (value == "1cup") myControl.pressLeftButton();
  else if (value == "2cup") myControl.pressRightButton();
  else if (value == "descale") myControl.pressLeftRightButton();
  return true;
}

/**
* Called by Homie upon an MQTT message to '.../buzzer'.
*/
bool buzzerHandler(const HomieRange& range, const String& value) {
  /**
  * Catch incorrect messages
  */
  if (value != "tone1" && value !="tone2" && value !="tone3" && value !="tone4") {
    senseoNode.setProperty("debug").send("buzzer: malformed message content. Allowed: [tone1,tone2,tone3,tone4].");
    return false;
  }

  if (!BuzzerSetting.get()) {
    senseoNode.setProperty("debug").send("buzzer: not configured.");
    return false;
  }

  senseoNode.setProperty("buzzer").send(value);
  if (value == "tone1") tone(beeperPin, 4096, 300);
  if (value == "tone2") tone(beeperPin, 2048, 300);
  if (value == "tone3") tone(beeperPin, 1536, 300);
  if (value == "tone4") tone(beeperPin, 1024, 300);
  senseoNode.setProperty("buzzer").send("");
  return true;
}

/**
* Senseo state machine, transition reaction: exit actions
*/
void senseoStateExitAction() {
  senseoNode.setProperty("debug").send(
    String("senseoState: Switching from ") + String(mySenseoSM.getStatePrevAsString())
    + String(" to ") + String(mySenseoSM.getStateAsString())
    + String(" after ") + String(mySenseoSM.getSecondsInLastState()) + String(" seconds")
  );
  switch (mySenseoSM.getStatePrev()) {
    case SENSEO_OFF: {
      senseoNode.setProperty("power").send("true");
      senseoNode.setProperty("outOfWater").send("false");
      senseoNode.setProperty("brew").send("false");
      break;
    }
    case SENSEO_HEATING: {
      break;
    }
    case SENSEO_READY: {
      break;
    }
    case SENSEO_BREWING: {
      senseoNode.setProperty("brew").send("false");
      // Determine brewed cup size based on time in brewing state
      int brewedSeconds = mySenseoSM.getSecondsInLastState();
      int brewedSize = 0;

      if (brewedSeconds <= 10) break;

      // 0---------------------|-----+-----|-----+-----|-------100
      int tolerance = (BrewHeat2CupSeconds - BrewHeat1CupSeconds) / 2;

      if (mySenseoSM.getState() == SENSEO_READY) {
        if (abs(brewedSeconds - BrewHeat1CupSeconds) < tolerance) {
          brewedSize = 1;
        }
        else if (abs(brewedSeconds - BrewHeat2CupSeconds) < tolerance) {
          brewedSize = 2;
        }
      }

      tolerance = (Brew2CupSeconds - Brew1CupSeconds) / 2;
      if (mySenseoSM.getState() == SENSEO_NOWATER || mySenseoSM.getState() == SENSEO_OFF) {
        if (abs(brewedSeconds - Brew1CupSeconds) < tolerance) {
          brewedSize = 1;
        }
        else if (abs(brewedSeconds - Brew2CupSeconds) < tolerance) {
          brewedSize = 2;
        }
      }

      senseoNode.setProperty("brewedSize").send(String(brewedSize));
      if (brewedSize == 0) {
        senseoNode.setProperty("debug").send("brew: Unexpected time in SENSEO_BREWING state. Please adapt timings.");
      }
      if (CupDetectorAvailableSetting.get() && myCup.isFilling()) myCup.setFull();
      break;
    }
    case SENSEO_NOWATER: {
      if (mySenseoSM.getState() != SENSEO_OFF) {
        senseoNode.setProperty("outOfWater").send("false");
      }
      break;
    }
    case SENSEO_unknown: {
      break;
    }
  }
}

/**
* Senseo state machine, transition reaction: entry actions
*/
void senseoStateEntryAction() {
  switch (mySenseoSM.getState()) {
    case SENSEO_OFF: {
      senseoNode.setProperty("brewedSize").send("0");
      senseoNode.setProperty("power").send("false");
      break;
    }
    case SENSEO_HEATING: {
      break;
    }
    case SENSEO_READY: {
      if (BuzzerSetting.get()) tone(beeperPin, 1536, 500);
      break;
    }
    case SENSEO_BREWING: {
      if (CupDetectorAvailableSetting.get()) {
        if (myCup.isAvailable()) {
          myCup.setFilling();
        }
        else {
          senseoNode.setProperty("debug").send("cup: Brewing without detected cup, will not report the filling->full process.");
        }
      }
      senseoNode.setProperty("brew").send("true");
      senseoNode.setProperty("brewedSize").send("0");
      break;
    }
    case SENSEO_NOWATER: {
      if (BuzzerSetting.get()) tone(beeperPin, 4096, 1800);
      senseoNode.setProperty("outOfWater").send("true");
      break;
    }
    case SENSEO_unknown: {
      break;
    }
  }
}

/**
* The device rebooted when attachInterrupt was called in setup()
* before Wifi was connected and interrupts were already coming in.
*/
void onHomieEvent(const HomieEvent &event) {
  switch (event.type) {
  case HomieEventType::WIFI_CONNECTED:
    attachInterrupt(digitalPinToInterrupt(ocSenseLedPin), ledChangedHandler, CHANGE);
    break;
  case HomieEventType::WIFI_DISCONNECTED:
    detachInterrupt(digitalPinToInterrupt(ocSenseLedPin));
    break;
  default:
    break;
  }
}

/**
*
*/
void setupHandler() {
  if (BuzzerSetting.get()) tone(beeperPin, 2048, 500);

  Homie.getLogger() << endl << "☕☕☕☕ Enjoy your SenseoWifi ☕☕☕☕" << endl << endl;

  senseoNode.setProperty("opState").send(mySenseoSM.getStateAsString());
  if (CupDetectorAvailableSetting.get()) {
    senseoNode.setProperty("cupAvailable").send(myCup.isAvailable() ? "true" : "false");
    senseoNode.setProperty("cupFull").send(myCup.isFull() ? "true" : "false");
  }
  senseoNode.setProperty("outOfWater").send("false");
  senseoNode.setProperty("brew").send("false");
  senseoNode.setProperty("debug").send("Machine started");
}

/**
*
*/
void loopHandler() {
  /**
  * Check and update the cup availability, based on the cup detector signal.
  * (no cup, cup available, cup full)
  */
  if (CupDetectorAvailableSetting.get()) {
    myCup.updateState();
    if (myCup.isAvailableChanged()) {
      senseoNode.setProperty("cupAvailable").send(myCup.isAvailable() ? "true" : "false");
    }
    if (myCup.isFullChanged()) {
      senseoNode.setProperty("cupFull").send(myCup.isFull() ? "true" : "false");
    }
  }

  /**
  * Update the low level LED state machine based on the measured LED timings.
  * (off, slow blinking, fast blinking, on)
  */
  mySenseoLed.updateState();
  if (mySenseoLed.hasChanged()) {
    if (true) Homie.getLogger() << "LED state machine, new LED state: " << mySenseoLed.getStateAsString() << endl;
  }

  /**
  * Update the higher level Senseo state machine based on the LED state.
  * (off, heating, ready, brewing, no water)
  */
  mySenseoSM.updateState(mySenseoLed.getState());
  if (mySenseoSM.stateHasChanged()) {
    if (true) Homie.getLogger() << "Senseo state machine, new Senseo state: " << mySenseoSM.getStateAsString() << endl;
    senseoNode.setProperty("opState").send(mySenseoSM.getStateAsString());

    senseoStateExitAction();
    senseoStateEntryAction();
  }

  /**
  * Non-blocking Low-High-Low transition.
  * Check for a simulated button press - release after > 100ms
  */
  myControl.releaseIfPressed();
}

void setup() {
  Serial.begin(115200);

  /**
  * Wemos D1 mini pin initializations
  */
  pinMode(ocPressLeftPin, OUTPUT);
  pinMode(ocPressRightPin, OUTPUT);
  pinMode(ocPressPowerPin, OUTPUT);
  pinMode(ocSenseLedPin, INPUT_PULLUP);

  digitalWrite(ocPressPowerPin, LOW);
  digitalWrite(ocPressLeftPin, LOW);
  digitalWrite(ocPressRightPin, LOW);

  pinMode(beeperPin, OUTPUT);
  pinMode(resetButtonPin, INPUT_PULLUP);

  if (CupDetectorAvailableSetting.get()) {
    pinMode(cupDetectorPin, INPUT_PULLUP);
    pinMode(cupDetectorAnalogPin, INPUT);
  }

  /**
  * Testing routine. Activate only in development environemt.
  * Tests the circuit and Senseo connections, loops indefinitely.
  *
  * Wifi will NOT BE AVAILABLE, no OTA!
  */
  if (false) testIO();


  /**
  * Homie specific settings
  */
  Homie_setFirmware("senseo-wifi", "1.8.1");
  Homie_setBrand("SenseoWifi");
  //Homie.disableResetTrigger();
  Homie.disableLedFeedback();
  Homie.setResetTrigger(resetButtonPin, LOW, 5000);
  Homie.setSetupFunction(setupHandler);
  Homie.setLoopFunction(loopHandler);

  /**
  * Homie: Options, see at the top of this file.
  */
  CupDetectorAvailableSetting.setDefaultValue(true);
  BuzzerSetting.setDefaultValue(true);

  /**
  * Homie: Advertise custom SenseoWifi MQTT topics
  */
  senseoNode.advertise("debug").setName("Debugging Information").setDatatype("string").setRetained(false);
  senseoNode.advertise("opState").setName("Operational State").setDatatype("enum").setFormat("SENSEO_unknown,SENSEO_OFF,SENSEO_HEATING,SENSEO_READY,SENSEO_BREWING,SENSEO_NOWATER");
  senseoNode.advertise("power").setName("Power").setDatatype("boolean").settable(powerHandler);
  senseoNode.advertise("brew").setName("Brew").settable(brewHandler).setDatatype("enum").setFormat("1cup,2cup");
  senseoNode.advertise("brewedSize").setName("Brew Size").setDatatype("string").setRetained(false);
  senseoNode.advertise("outOfWater").setName("Out of Water").setDatatype("boolean");
  if (CupDetectorAvailableSetting.get()) senseoNode.advertise("cupAvailable").setName("Cup Available");
  if (CupDetectorAvailableSetting.get()) senseoNode.advertise("cupFull").setName("Cup Full");
  if (BuzzerSetting.get()) senseoNode.advertise("buzzer").setName("Buzzer").settable(buzzerHandler).setDatatype("enum").setFormat("tone1,tone2,tone3,tone4");

  if (BuzzerSetting.get()) tone(beeperPin, 1536, 2000);
  Homie.onEvent(onHomieEvent);
  Homie.setup();
}

void loop() {
  Homie.loop();
}

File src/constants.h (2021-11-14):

/*
  config.h - Configuration for the SenseoWifi project.
  Created by Thomas Dietrich, 2016-03-05.
  Released under some license.
*/

#ifndef SenseoConstants_h
#define SenseoConstants_h

// LED state machine
// Measure your timings by activating debugging in ledChangedRoutine()
static const int pulseDurLedSlow = 1000;                   // duration of one pulse when LED is blinking slow in milliseconds (state LED_SLOW)
static const int pulseDurLedFast = 100;                    // duration of one pulse when LED is blinking fast in milliseconds (state LED_FAST)
static const int pulseDurTolerance = 10;                   // tolerance for pulse duration. With the tested senseo, tolerance was not more than +-1ms
static const int pulseContThreshold = 2 * pulseDurLedSlow; // time before switching to continuous LED state (state LED_ON and state LED_OFF)

// Senseo state machine (in seconds)
static const int HeatingTime = 70;
static const int HeatingTimeTol = 15;
static const int Brew1CupSeconds = 21;
static const int Brew2CupSeconds = 41;
static const int BrewHeat1CupSeconds = 55;
static const int BrewHeat2CupSeconds = 85;

// Debouncing (in milliseconds)
static const int CupDebounceInterval = 500;
static const int LedIgnoreChangeDuration = 5;

// Duration of button "press" (in milliseconds)
static const int pressDuration = 150;

#endif

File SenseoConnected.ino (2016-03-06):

/*
  SenseoConnected.ino - base file for the SenseoWifi project.
  Created by Thomas Dietrich, 2016-03-05.
  Released under some license.
*/

#include "SenseoLed.h"
#include "SenseoSM.h"
#include "Cup.h"
#include "config.h"

#include <ESP8266WiFi.h>
#include <PubSubClient.h>

SenseoLed mySenseoLed(ocSenseLedPin);
SenseoSM mySenseoSM;
Cup cup(cupDetectorPin, beeperPin);

const char *ssid =  "xxxxxxxxxx";    // cannot be longer than 32 characters!
const char *pass =  "xxxxxxxxxx";   //
IPAddress server(85, 119, 83, 194);

WiFiClient wclient;
PubSubClient client(wclient, server);


void ledChangedRoutine() {
  // will get called by the LED changed interrupt
  mySenseoLed.pinStateToggled();

  // Debugging and Setup: Uncomment the following to get LED pulse durations
  //Serial.print("LED pulse duration: ");
  //Serial.println(mySenseoLed.getLastPulseDuration());
}

void cupDetectorRoutine() {
  //debounce!?
  cup.updateState();
  //Serial.print("Cup Detector: ");
  //Serial.println(cup.getState());
}


String subMsg = "";

void callback(const MQTT::Publish& pub) {
  //Serial.print(pub.topic());
  //Serial.print(": ");
  if (pub.has_stream()) {
    Serial.println("(too long)");
  } else
    subMsg = pub.payload_string();
  //Serial.println(pub.payload_string());
}


void WiFiMQTTConnect() {
  if (WiFi.status() != WL_CONNECTED) {
    Serial.print("Connecting to ");
    Serial.print(ssid);
    Serial.println("...");
    WiFi.begin(ssid, pass);

    if (WiFi.waitForConnectResult() != WL_CONNECTED)
      return;
    Serial.println("WiFi connected");
  }
  
  if (WiFi.status() == WL_CONNECTED) {
    if (!client.connected()) {
      if (client.connect("arduinoClient")) {
        Serial.println("Connected to MQTT server");
        client.set_callback(callback);
        client.publish("SenseoConnected/w66a/msg", "Senseo Connected! :)");
        client.subscribe("SenseoConnected/w66a/command");
      }
    }
    if (client.connected()) client.loop();
  }
}


void testIO() {
  Serial.println("\n=======================");
  Serial.println("   Hello Senseo :)");
  Serial.println("   (testing all inputs and outputs)");
  Serial.println("=======================");
  while (true) {
    Serial.print("\nCup: ");
    Serial.print(!digitalRead(cupDetectorPin));
    Serial.print(" (");
    Serial.print(analogRead(cupDetectorAnalogPin));
    Serial.print(")   Senseo status LED: ");
    Serial.print(!digitalRead(ocSenseLedPin));
    Serial.println();
    delay(2000);

    Serial.println("Testing Beeper ...");
    tone(beeperPin, 1024, 1000);
    delay(2000);

    if (0) {
      Serial.println("Testing On/Off Button ...");
      digitalWrite(ocPressPowerPin, HIGH);
      delay(200);
      digitalWrite(ocPressPowerPin, LOW);
      delay(2000);
    }

    if (0) {
      Serial.println("Testing Left Button ...");
      digitalWrite(ocPressLeftPin, HIGH);
      delay(200);
      digitalWrite(ocPressLeftPin, LOW);
      delay(2000);
    }

    if (0) {
      Serial.println("Testing Right Button ...");
      digitalWrite(ocPressRightPin, HIGH);
      delay(200);
      digitalWrite(ocPressRightPin, LOW);
      delay(2000);
    }
  }
}


void setup() {
  Serial.begin(9600);

  pinMode(ocPressLeftPin, OUTPUT);
  pinMode(ocPressRightPin, OUTPUT);
  pinMode(ocPressPowerPin, OUTPUT);
  pinMode(ocSenseLedPin, INPUT_PULLUP);

  pinMode(cupDetectorPin, INPUT_PULLUP);
  pinMode(cupDetectorAnalogPin, INPUT);
  pinMode(beeperPin, OUTPUT);

  digitalWrite(ocPressPowerPin, LOW);
  digitalWrite(ocPressLeftPin, LOW);
  digitalWrite(ocPressRightPin, LOW);

  attachInterrupt(digitalPinToInterrupt(ocSenseLedPin), ledChangedRoutine, CHANGE);
  attachInterrupt(digitalPinToInterrupt(cupDetectorPin), cupDetectorRoutine, CHANGE);

  Serial.println("\n");

  // uncomment to test your circuit and Senseo connections
  //testIO();
}


void loop() {
  WiFiMQTTConnect();

  mySenseoLed.updateState();
  if (mySenseoLed.hasChanged()) {
    Serial.print("LED state machine, new LED state: ");
    Serial.println(mySenseoLed.getStateAsString());
  }

  mySenseoSM.updateState(mySenseoLed.getState());
  if (mySenseoSM.stateHasChanged()) {
    Serial.print("Senseo state machine, new Senseo state: ");
    Serial.print(mySenseoSM.getStateAsString());
    Serial.print(" (time in old state: ");
    Serial.print(mySenseoSM.getTimeInLastState());
    Serial.print("s)\n\n");
  }

  if (mySenseoSM.stateHasChanged()) {
    String s = "in last state: ";
    client.publish("SenseoConnected/w66a/time", s + mySenseoSM.getTimeInLastState());
    client.publish("SenseoConnected/w66a/state", mySenseoSM.getStateAsString());
  }

  if (mySenseoSM.stateHasChanged()) {
    if (mySenseoSM.getState() == SENSEO_READY) {
      tone(beeperPin, 1024, 500);
    }
    if (mySenseoSM.getState() == SENSEO_NOWATER) {
      tone(beeperPin, 2048, 1000);
    }
  }

  if (subMsg != "") {
    Serial.print("Nachricht: ");
    Serial.println(subMsg);
    if (subMsg == "ON") {
      if (mySenseoSM.getState() == SENSEO_OFF) {
        digitalWrite(ocPressPowerPin, HIGH);
        delay(100);
        Serial.println("MQTT: command accepted");
        client.publish("SenseoConnected/w66a/response", "accepted");
        digitalWrite(ocPressPowerPin, LOW);
      }
    } else if (subMsg == "OFF") {
      if (mySenseoSM.getState() != SENSEO_OFF) {
        digitalWrite(ocPressPowerPin, HIGH);
        delay(100);
        Serial.println("MQTT: command accepted");
        client.publish("SenseoConnected/w66a/response", "accepted");
        digitalWrite(ocPressPowerPin, LOW);
      }
    } else if (subMsg == "1-cup") {
      if (mySenseoSM.getState() == SENSEO_READY) {
        digitalWrite(ocPressLeftPin, HIGH);
        delay(100);
        Serial.println("MQTT: command accepted");
        client.publish("SenseoConnected/w66a/response", "accepted");
        digitalWrite(ocPressLeftPin, LOW);
      }
    } else if (subMsg == "2-cup") {
      if (mySenseoSM.getState() == SENSEO_READY) {
        digitalWrite(ocPressRightPin, HIGH);
        delay(100);
        digitalWrite(ocPressRightPin, LOW);
        Serial.println("MQTT: command accepted");
        client.publish("SenseoConnected/w66a/response", "accepted");
      }
    } else {
      Serial.println("MQTT: unknown command");
      client.publish("SenseoConnected/w66a/response", (String)("unknown command" + subMsg));
    }
    subMsg = "";
  }
}

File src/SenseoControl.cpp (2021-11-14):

/*
SenseoControl.cpp - Library for the SenseoWifi project.
Created by Thomas Dietrich, 2016-03-05.
Released under some license.
*/

#include "SenseoControl.h"

SenseoControl::SenseoControl(int pBPin, int lBPin,  int rBPin) {
  powerButtonPin = pBPin;
  leftButtonPin = lBPin;
  rightButtonPin = rBPin;
}

void SenseoControl::pressPowerButton() {
  digitalWrite(powerButtonPin, HIGH);
  timestampPressed = millis();
}

void SenseoControl::pressLeftButton() {
  digitalWrite(leftButtonPin, HIGH);
  timestampPressed = millis();
}

void SenseoControl::pressRightButton() {
  digitalWrite(rightButtonPin, HIGH);
  timestampPressed = millis();
}

void SenseoControl::pressLeftRightButton() {
  digitalWrite(leftButtonPin, HIGH);
  digitalWrite(rightButtonPin, HIGH);
  timestampPressed = millis();
}

/**
 * The 'press..Button()' functions will "press" but not release the buttons.
 * Call this method regularly (every loop() run) to release buttons after some time.
 */
void SenseoControl::releaseIfPressed() {
  if ((timestampPressed != 0) && (millis() - timestampPressed >= pressDuration)) {
    digitalWrite(powerButtonPin, LOW);
    digitalWrite(leftButtonPin, LOW);
    digitalWrite(rightButtonPin, LOW);
    timestampPressed = 0;
  }
}

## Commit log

2016-03-05 first commit
    includes Circuit Testing, LED Interrupt and LED state machine
2016-06-21 Add finished fritzing PCB projects
    [SenseoWifi-PCB.fz]
2016-07-09 Add final PCB design
    [SenseoWifi-PCB.fz]
2016-12-31 Change PCB flaws of v1.6 order
    [SenseoWifi-PCB.fz]
2017-01-01 Fix reset bug with workaround
    [SenseoWifi.cpp, pins.h, testIO.cpp]
2017-01-01 First improvements to button pressing, not working
    [SenseoWifi.cpp, testIO.cpp]
2017-01-06 Add non-blocking button presses, comments
2017-01-06 Add simple LED debouncer, minor changes
2017-01-07 Replace Bounce2 by own implementation, add constants
    [SenseoControl.cpp, SenseoLed.cpp, SenseoWifi.cpp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]
2017-01-08 Switch state entry and exit actions
2017-12-26 Fix various bugs and inconsistencies
    [SenseoLed.cpp, SenseoWifi.cpp]
2017-12-27 Add PCB real picture
2018-07-16 Add VCC-G header and Gerber exports
    [SenseoWifi-PCB.fz]
2019-07-22 Rework on docs (#21)
    * * Adding configuration of serial port
    * fixing espressif8266 to 2.0.4 (see https://forum.blueforcer.de/d/262-trouble-to-compile-the-firmware )
    * longer button-press
    changing pressDuration for better reliability
    * rework on README.md
    Adding some examples for openhab-config.
    * fixing little typo
    * More about building
    Adding information about tools for building firmware
    * fixing seems not to be necessary
    * necessary after all
    * Headline & filler sentence
    Adding suggested changes
    * avoid invalid default configuration
    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
    [constants.h]
2020-02-08 Add power consumption to README
2020-02-10 Add all dedicated pin headers to PCBv1.8, improve hardware steps
    [SenseoWifi-PCB.fz]
2020-02-10 Rename assembled PCB image
2020-05-07 Fix platform version for arduino core (#28)
2020-05-11 Improve LED interrupt handling (#30)
    * Changed Led interrupt handling to ICACHE_RAM_ATTR. Works with actual espressi8266 2.7.1, changed platformio.ini to get actual version of espressi8266 (#29)
    * Homie.event forgotten, fixed
    * removed unnecessary declaration and changed sourcecode-format to match with the original
    [SenseoWifi.cpp]
2021-10-04 Add buzzer command, add HA example, update Homie lib
    [SenseoWifi.cpp]
2021-10-04 Add PCB v1.8 gerber export
2021-10-14 Fix #46 non-existing cup set to full at end of brew
    [SenseoWifi.cpp]
2021-11-04 Make debug topic more chatty, avoid deleting the topic
    [SenseoWifi.cpp]
2021-11-14 Increase expected heating time
2021-12-06 Reset brewed_size after some time
    [SenseoWifi.cpp]
2023-02-18 Fix buzzer duration conflict w LED state machine
    In no water state, the LED blinks at approx 100ms. The no water buzzer blocks the LED interrupts, which leads to more than 2000ms, interpreted as LED_ON or LED_OFF. This change is a simple fix/workaround to avoid this special case. Generally the Buzzer should not interrupt the LED detector - however, so far this was no issue, so will not make a big deal about it.
    It is not clear to me, why this problem came up with a new machine today, and never before.
    [SenseoWifi.cpp]
